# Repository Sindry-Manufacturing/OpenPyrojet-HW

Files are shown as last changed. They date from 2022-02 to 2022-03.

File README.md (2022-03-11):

# OpenPyrojet-HW
This is a repository for the hardware components of the OpenPyrojet 3D printer project. 
The current objective of OpenPyrojet, is  to create the first generation Open source/hardware/software thermal spraying 3D printer. 
In short, by using affordable, accessible and readily available parts and materials, we will create a new breed of 3D printer, that enables the heterogenous additive manufacturing of metal, plastic and ceramic monoliths rapidly, precisely, autonomously and at relatively low cost(in terms of time and money) to the user compared to contemporary 3D printing solutions. 

We believe this to be possible, due to the convergence of several co-factors in the present day(2022). In particular, the incredible decline in cost and complexity of autonomous CNC and robotic components, in terms of control and actuation, as well as the wide availability of good quality standard structural elements, the decreasing cost of refractory materials in favorble form factors, the wide availability of energy dense fuel products, and the increasing availability and declining cost of particulate material feedstocks. 
Additionally, the need for low cost, autonomous and widely accessible electronics prototyping and manufacturing processes, that improve on the user experience and the overall dirty dull and dangerous state of the art in electronics manufacturing are highly desirable to many parties beyond just we the developers. Current 3D printing approaches are largely ineffective in terms of cost and time for generating high quality, looks like, feels like, and works like, electronic parts, we believe this represetns a substantial opportunity to create change in electronics manufacturing and prototyping, and eventually in the whole of manufacturing as a concept through the introduction of relatively low cost, autonomous, high speed, high precision 3D printing of metals, plastics and ceramics. 
We also aim to eventually bring totally custom, free open and autonomous, on demand manufacturing, to the consumer desktop, or at least to the community scale, facilitating a return to the flexible and local cottage industries of the past, now cybernetically enhanced with the ability to create with the speed and quality of autonomous mass production assembly lines, and accelerated by the computerization and networked intelligence of the modern internet. 

We believe we can accomplish these lofty goals by hybridizing thermal inkjet printing and thermal spray tehnologies into a compact, self contained, open source 3D printer print head assembly and material feedstock handling system integrable with mass market consumer 3D printer control boards and robotic motion systems such as the Ender 3, the Prusa mk3s and mini, and others. 

The basic system concept is thus:
Fuel and material are held in a reservoir, kept mixed and pumped in and out by a syringe pump. This pump pushes fuel, and suspended material particles to the print head from the back through perfboard(of which the print head is made) holes. The fuel and material mixture circulate over the top of the print head at a constant average velocity to produce a negative pressure and prevent settling of the materials suspended in the fuel.
When the time comes to deposit material on the build plate, a short voltage pulse of controlled amplitude is applied to the captive heater wire, across two adjacent plated through vias in the perfboard.  This causes the wire to rapidly(with in 1-10 milliseconds) heat up, vaporizing the fuel and entraining the suspended material. 
Once an appropriate volume of fuel and material has been vaporized into the nozzle, a second, larger amplitude voltage pulse is applied, raising the temperature in the nozzle to the autoignition temperature of the fuel/air mixture in the nozzle. This ignites the fuel-air mixture, and melts and accelerates the material to deposit it on the build plate. Thusly, can we deposit virtually any material known, heterogenously, autuonomously with nearly complete closed loop control of the mass and energy flows of the process. 
Control is achieved by continuously performing 3 simultaneous measurement techniques, namely, differential scanning calorimetry(DSC), Surface enhanced IR spectroscopy(IRSPEC), and cyclcic voltammetry(CV). 
The first technique(DSC) is done by continuously monitoring the relationship between temperature, and power of the heating element throughout the deposition process. By tracking changes in the power applied to the element to maintain a given temperature across the whole temperature ramp during deposition, we can spot phase changes, ignition, deflagration and combustion, and continuously monitor the health and efficiency of the deposition proces in each nozzle during each discrete deposition event.  
The second technique (IRSPEC) is done by continuously monitoring the short time scale photocurrents induced in the element by the emitted and reflected ir-photons fromthe combustion ofthe fuel, the melting and cooling of the feed stock material and from te various surfaces effected during deposition. This allows us to monitor the chemical composition of the involved surfaces in real time, and to get a handle on the specic bonding events taking place to allow tunig and monitoring of interface growth and quality during deposition.
The third technique(CV) is done by providing a controlled input voltage waveform, and continuously monitoring changes in the response current of the heating element and adjoining electrical contacts. In this way we can detect electrochemical events and manipulate the electrochemistry of the combustion, and gaseous phases in the vicinity of the deposition process, in particular, oxidation events, reduction events, partial combustion, coking, etc.

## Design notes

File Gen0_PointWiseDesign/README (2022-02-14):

This is a repository dedicated to hardware for FDM printer mods that enable direct printing of metal, plastic, and ceramic through conventional FDM style cartesian printers and their associatedpoint wise scanning design.
Essentially, we pump air through a carburetor which contains metal/ceramic/plastic loaded fuel (ethanol, gasoline etc.) this entrains particles of the material in droplets of the fuel into the pumped airstream and sends them to 
a conventional E3D extruder hotend which ignites the fuel mixture and enables a continuous flame spray like deposition process, controlled by an FDM printer cartesian stage to form 3D dimensional objects in a continuous machine path, layer by layer.

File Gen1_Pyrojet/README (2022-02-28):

This is a repository for images, video and information regarding th first generation (96 DPI) FR4 based inkjet style pyrojet printer built on a modified ender3 platform. 
This includes hardware design guides, introductory texts on the construction and operation of the system and in depth technical data reagarding materials, lifetime, and printing capabilities. 

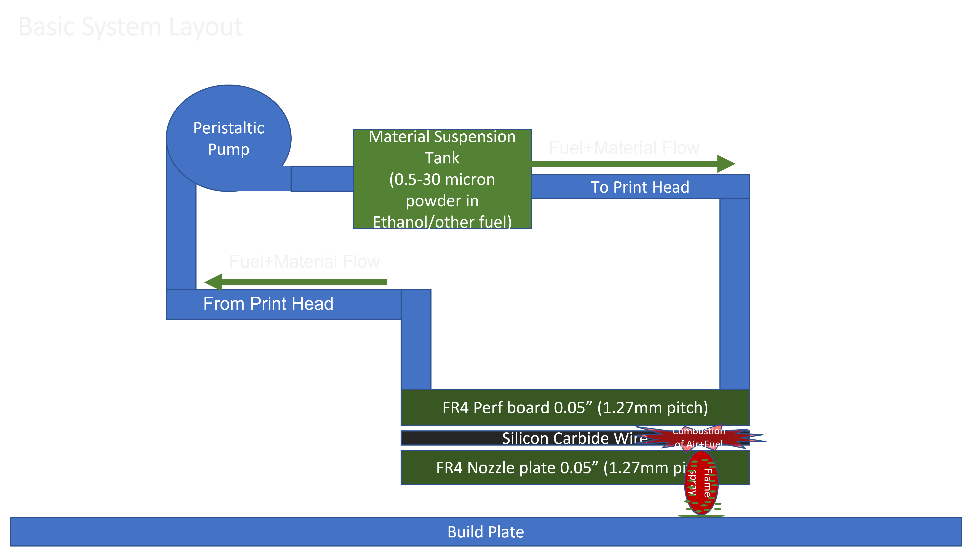
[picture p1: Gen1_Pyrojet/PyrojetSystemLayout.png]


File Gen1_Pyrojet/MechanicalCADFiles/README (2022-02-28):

This is where you can find the adapters for the generation 1 pyrojet print head. It is designed to be adaptable to the main gantry plate of the Ender 3 FDM 3D printer from creality.

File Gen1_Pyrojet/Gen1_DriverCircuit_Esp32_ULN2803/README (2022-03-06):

This is a directory for images and CAD files relating to the driver electronics for the first generation Pyrojet print head

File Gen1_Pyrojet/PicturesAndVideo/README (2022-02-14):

This is a directory for containing images and video of the generation 1 inkjet style pyrojet print heads.

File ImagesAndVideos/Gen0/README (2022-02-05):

This is a directory of the old images and videos pertaining to the Generation 0 print head design...

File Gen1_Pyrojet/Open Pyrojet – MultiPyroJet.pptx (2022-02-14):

## Open Pyrojet – MultiPyroJet

FDM printer modified to print metal, ceramic and high temperature plastics, with enhanced resolution, automation, control and speed.

## Basic System Layout

Build Plate

Peristaltic Pump

Material Suspension Tank
(0.5-30 micron powder in Ethanol/other fuel)

Fuel+Material Flow

To Print Head

Fuel+Material Flow

From Print Head

FR4 Perf board 0.05” (1.27mm pitch)

Silicon Carbide Wire

FR4 Nozzle plate 0.05” (1.27mm pitch)

Combustion of Air+Fuel

Flame spray

## Print Head Detail

The print head is made with an FR4 pefboard as the backplate, serving as electrical connection and mechanical support to a silicon carbide wire. This wire, once mechanically clamped across the plated through holes in the perfboard, via compression by a milled FR4 copper clad nozzle plate, acts as a heating element that ejects fuel and material through the milled nozzles.

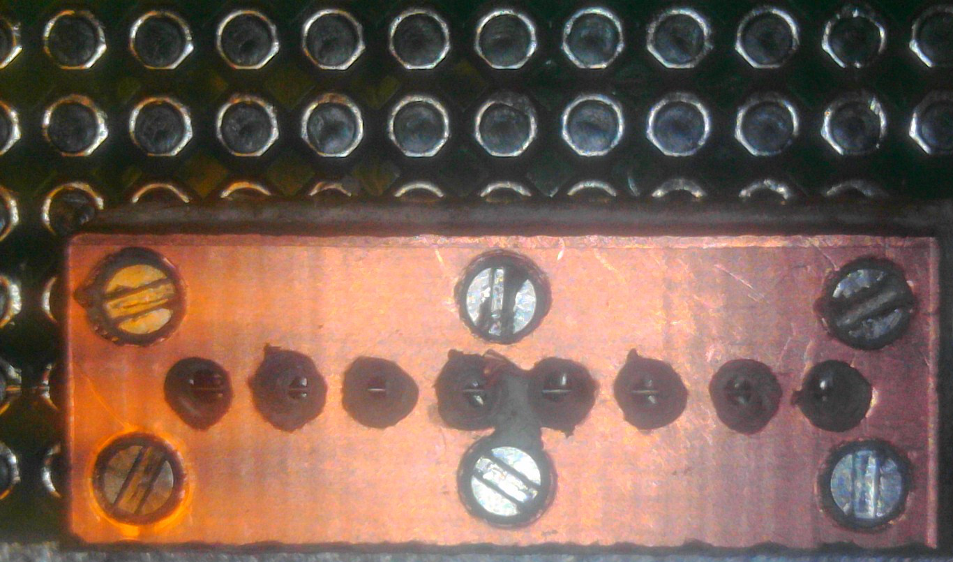
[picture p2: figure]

1.27 mm Perf Board

CNC milled copper clad FR4 nozzle plate

Silicon Carbide Wire

0.3mm Nozzle

M0.6X4mm Screw

0.65mm diameter hole, 1mm pad diameter

## Basic System Description_MultiPyrojet-

1. Fuel and material are held in a reservoir, kept mixed and pumped in and out by a single peristaltic pump. This peristaltic pump pushes fuel, and suspended material particles to the print head from the back through the perfboard holes. The fuel and material mixture circulate over the top of the print head at a constant average velocity to produce a negative pressure and prevent leakage from the print head.
2. When the time comes to deposit material on the build plate, a short voltage pulse of controlled amplitude is applied to the captive silicon carbide wire, across two adjacent plated through vias in the perfboard. This causes the wire to rapidly heat up, vaporizing the fuel and entraining the suspended material.
3. Once an appropriate volume of fuel and material has been vaporized into the nozzle, a second, larger amplitude voltage pulse is applied, raising the temperature in the nozzle to the autoignition temperature of the fuel/air mixture in the nozzle. This ignites the fuel-air mixture, and melts and accelerates the material to deposit it on the built plate.

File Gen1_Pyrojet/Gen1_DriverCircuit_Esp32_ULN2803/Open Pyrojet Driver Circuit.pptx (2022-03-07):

## Open Pyrojet Driver Circuit

By Michal Lynn

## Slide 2

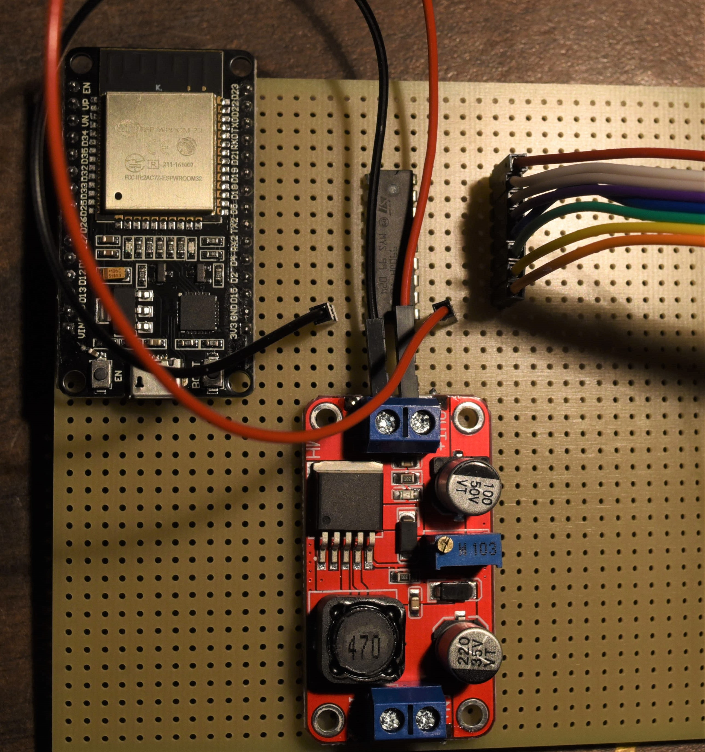
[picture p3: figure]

ESP 32

ULN2803A Darlington array

XL6019 Converter

Outputs

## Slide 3

Datasheets for assorted components-

https://www.ti.com/product/ULN2803A
https://datasheetspdf.com/pdf/839862/Xlsemi/XL6019/1
https://www.google.com/url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
https://www.mouser.com/datasheet/2/58/BPS-DAT-(ST3U)-Datasheet-771561.pdf

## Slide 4

Datasheets for assorted components-

Print Head

SiC Filament

ESP32

3-5 V Digital PWM Output

ULN2803A
(2)

+ 40 Volts

Ground

XL6019

+ 12/24 Volts

Ground

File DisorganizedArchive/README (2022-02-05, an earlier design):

This is a directory of all the old files and iterations on the way to version 1 hardware...This is only provided for reference material for curious adventurers, and as reference materials for future iterations...

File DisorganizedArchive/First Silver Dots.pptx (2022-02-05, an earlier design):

## First Silver Dots

10% mass loading of silver in 90% WD-40
1-3 Micron average diameter silver particles
Printed with ~12 watts of peak input power (manually controlled)

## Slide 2

0.75mm

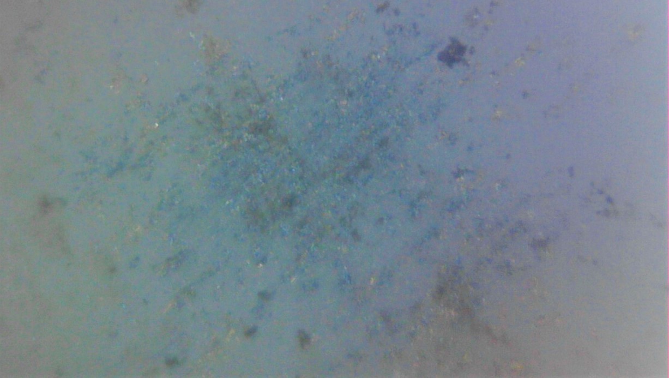
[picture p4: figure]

< 10 micron thick Silver deposit

0.75mm

Al2O3 Substrate

Single pulse deposit

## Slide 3

1.5mm

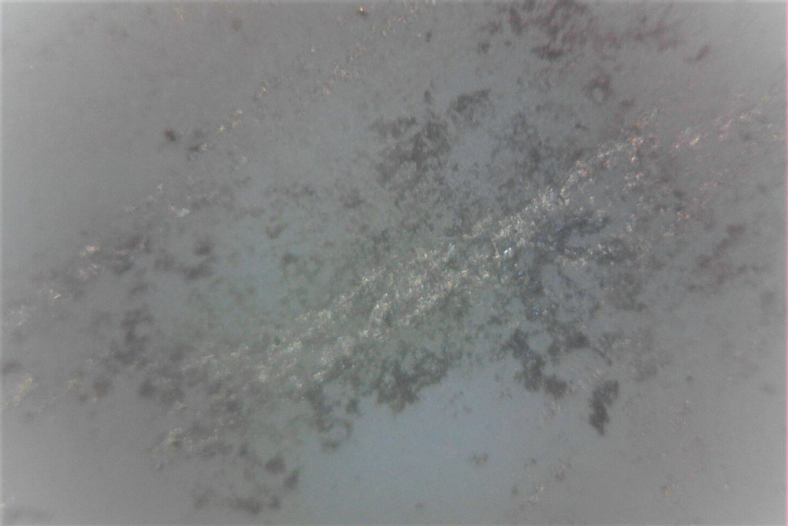
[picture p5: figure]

Steel needle scratch zone

< 10 micron thick Silver deposit

1.0mm

Al2O3 Substrate

Two pulse deposit

Print Direction

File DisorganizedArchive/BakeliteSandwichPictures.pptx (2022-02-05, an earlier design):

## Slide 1

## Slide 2

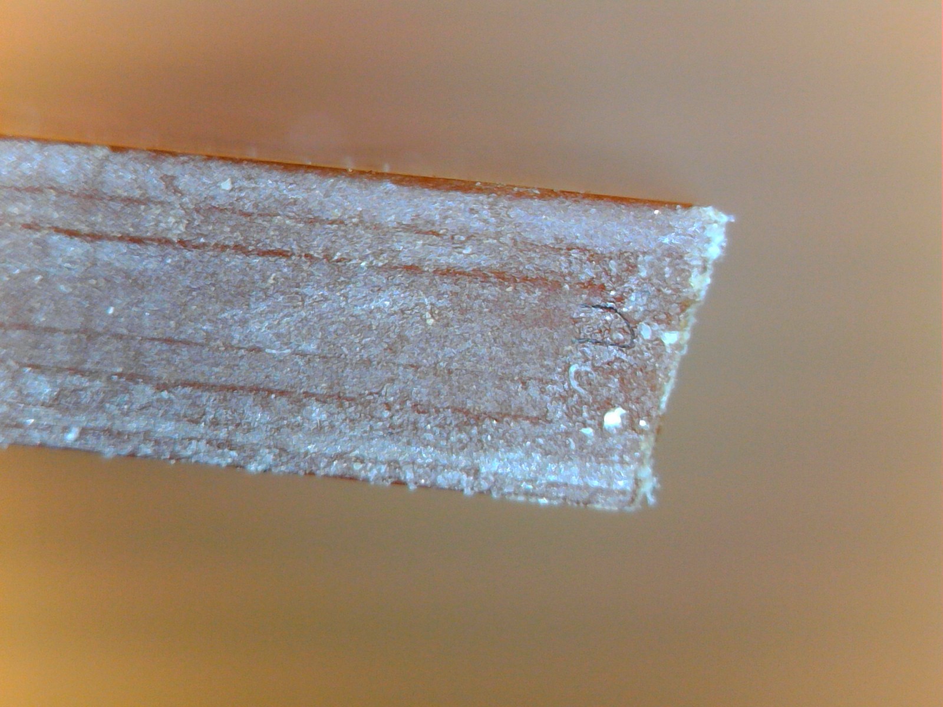
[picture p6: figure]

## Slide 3

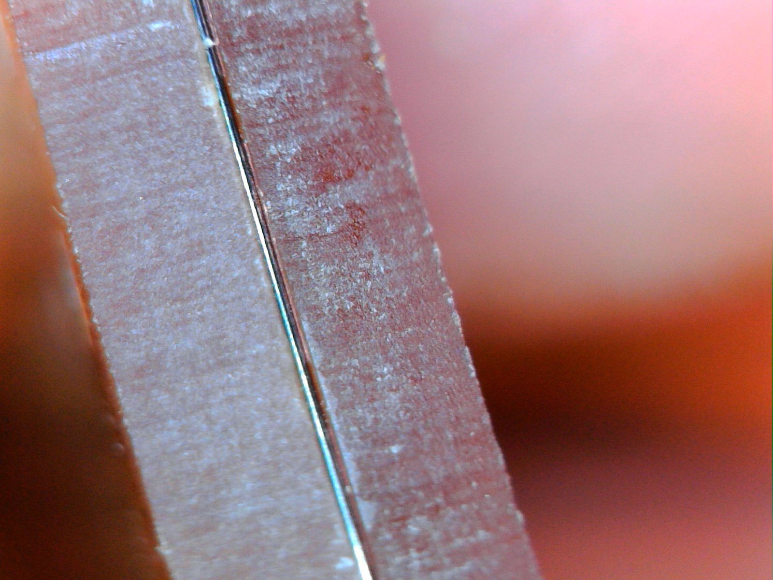
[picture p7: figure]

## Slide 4

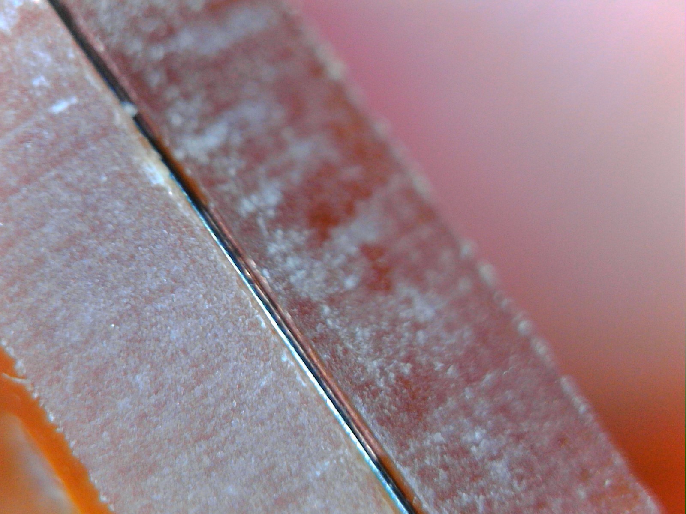
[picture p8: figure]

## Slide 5

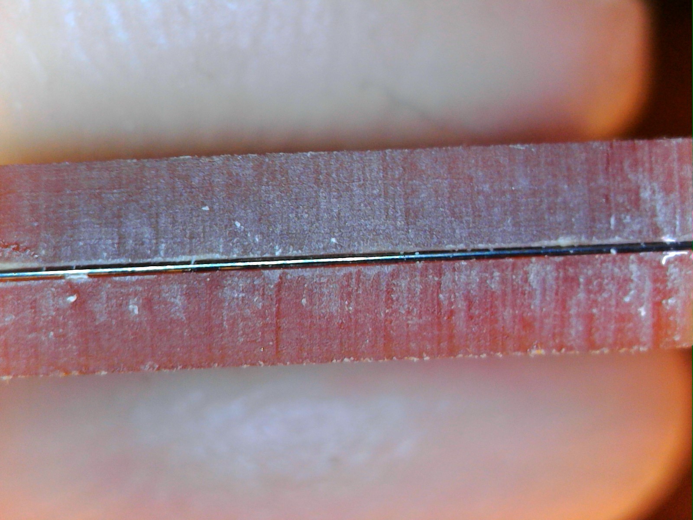
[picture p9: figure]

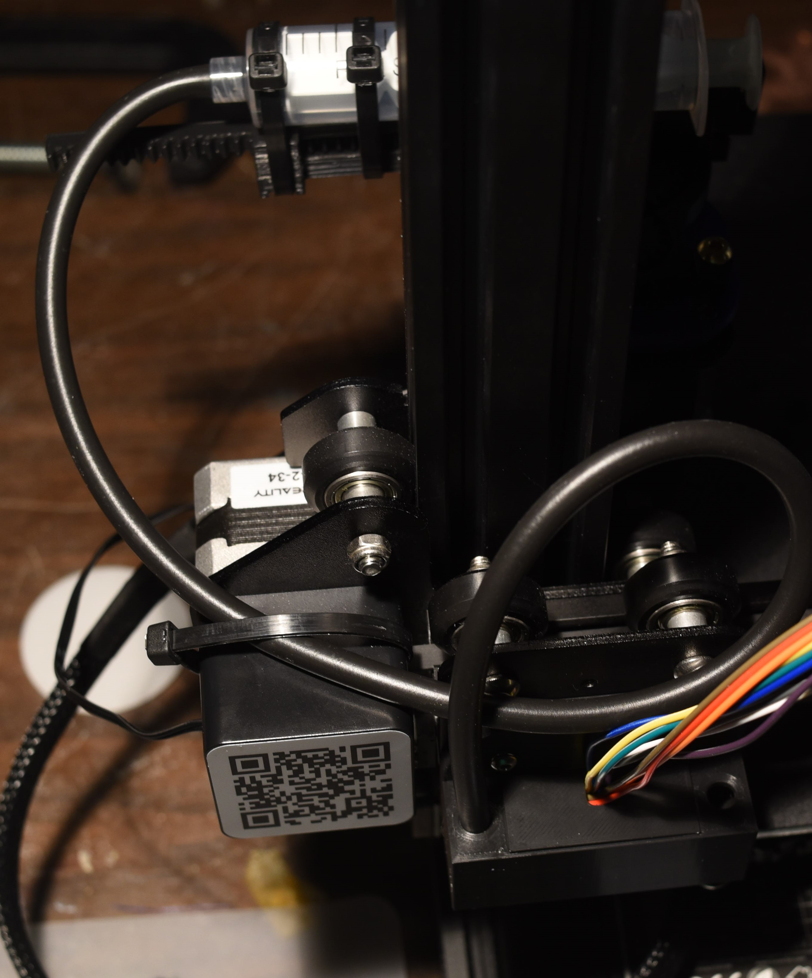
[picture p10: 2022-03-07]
Gen1_Pyrojet/MechanicalCADFiles/SyringePumpFuelController_4.jpg

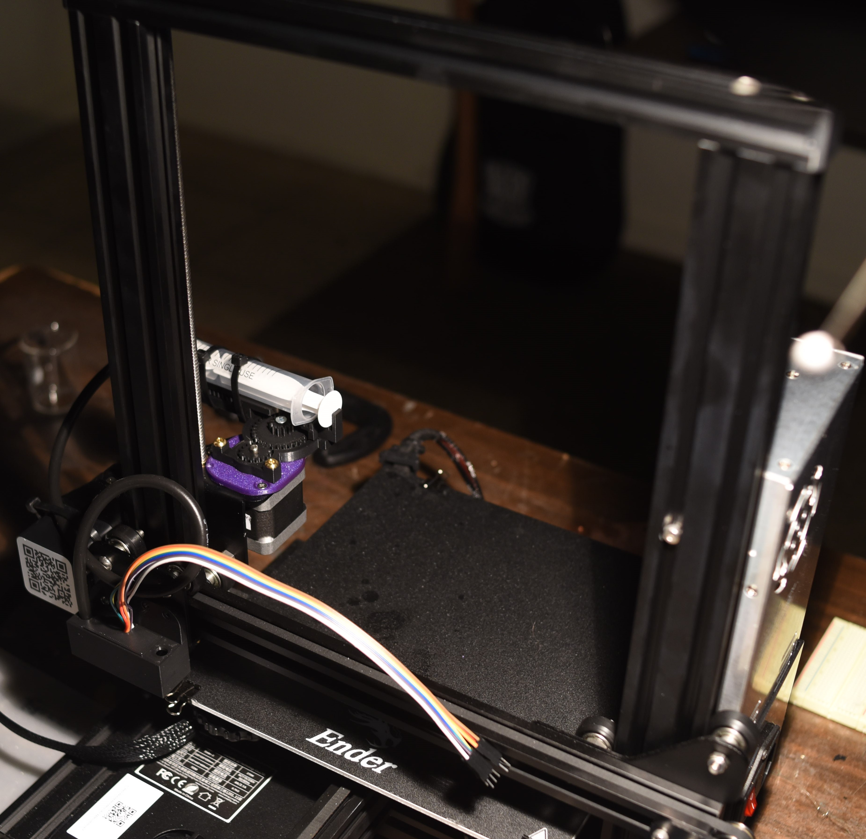
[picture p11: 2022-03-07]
Gen1_Pyrojet/MechanicalCADFiles/SyringePumpFuelController_5.jpg

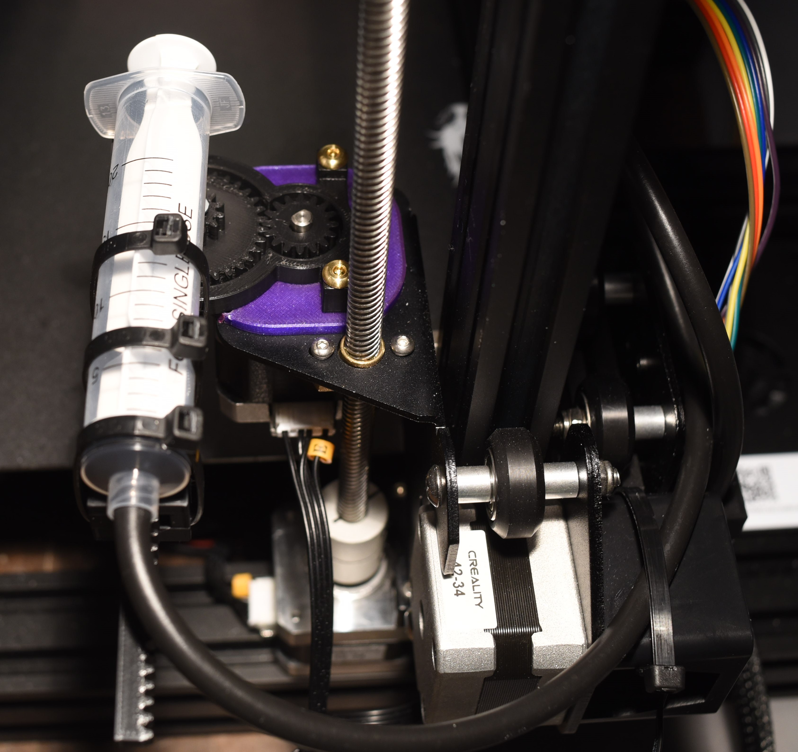
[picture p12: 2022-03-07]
Gen1_Pyrojet/MechanicalCADFiles/SyringePumpFuelController_3.jpg

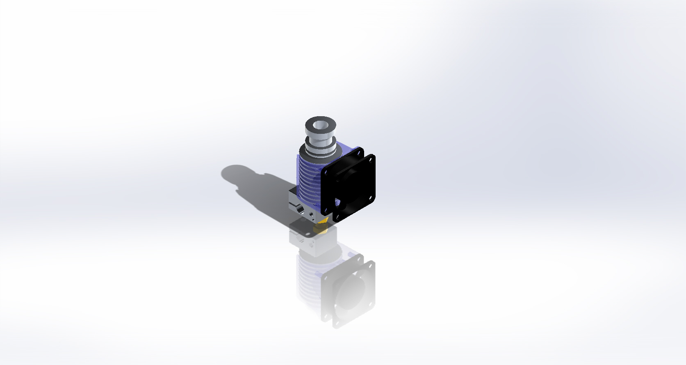
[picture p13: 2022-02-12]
Gen0_PointWiseDesign/e3d v6.JPG

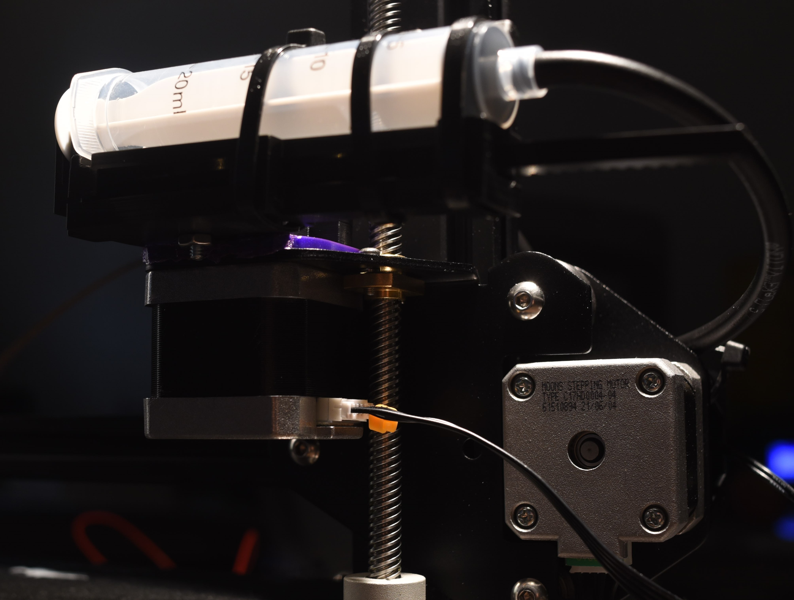
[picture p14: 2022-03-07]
Gen1_Pyrojet/MechanicalCADFiles/SyringePumpFuelController_2.jpg

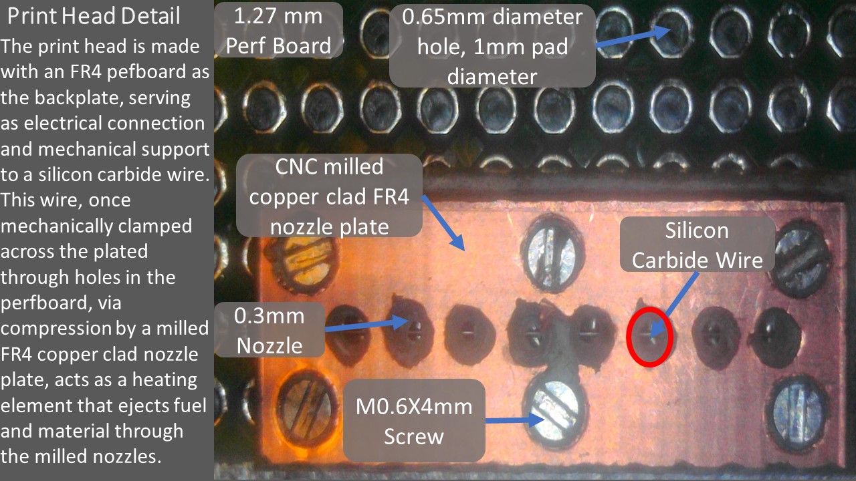
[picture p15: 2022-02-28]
Gen1_Pyrojet/PicturesAndVideo/CloseupOfNozzlePlateOverview.JPG

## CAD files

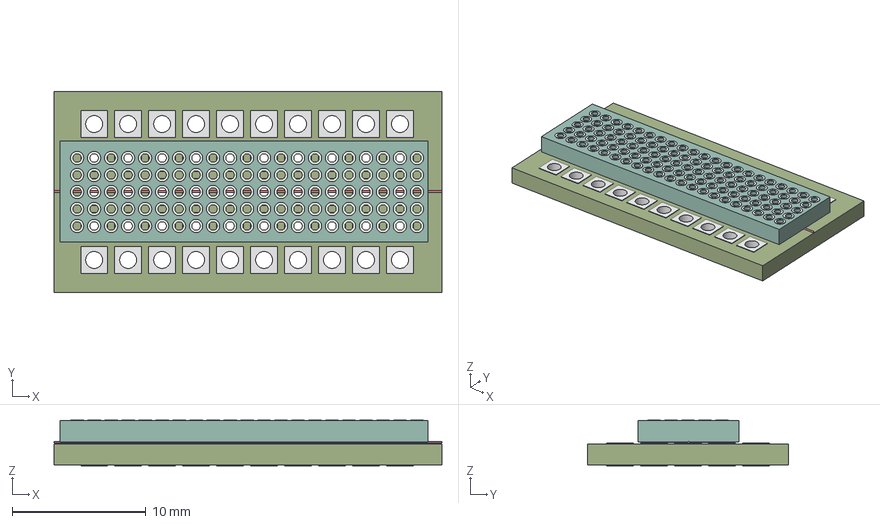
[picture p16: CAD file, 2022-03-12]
Gen1_Pyrojet/MechanicalCADFiles/PrintheadV1Assembly1.stp
29.0 x 15.0 x 3.41 mm
2.54mmPitchPerfboardBackplane
1.27mmNozzlePlate
SiCFilamentRed

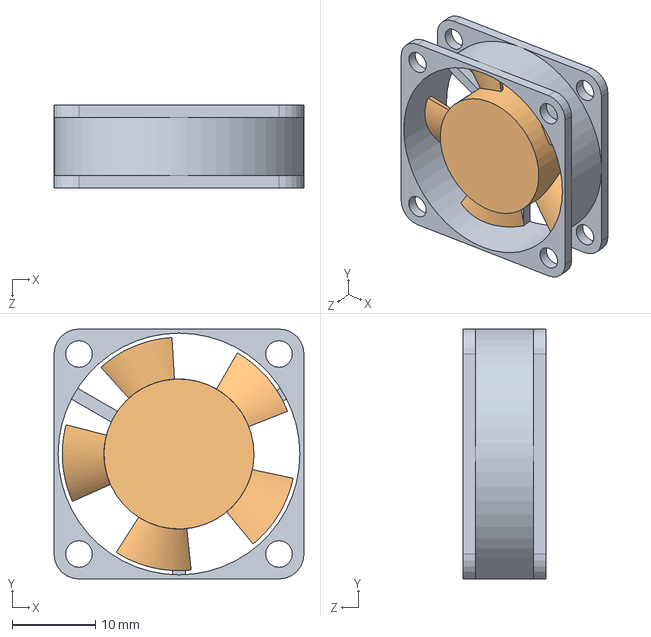
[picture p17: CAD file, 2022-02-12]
Gen0_PointWiseDesign/fan.SLDASM
30.0 x 30.0 x 10.0 mm
fan sub1
fan sub2

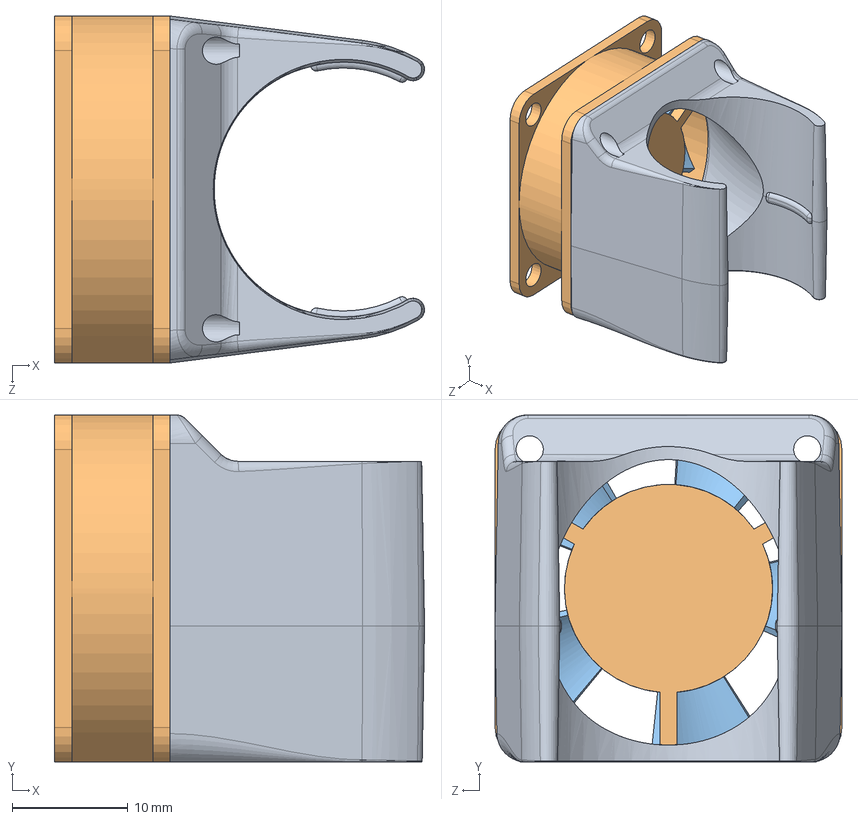
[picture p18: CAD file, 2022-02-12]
Gen0_PointWiseDesign/fanduct.SLDASM
32.0 x 30.0 x 30.0 mm
fan duct
fan sub1
fan sub2

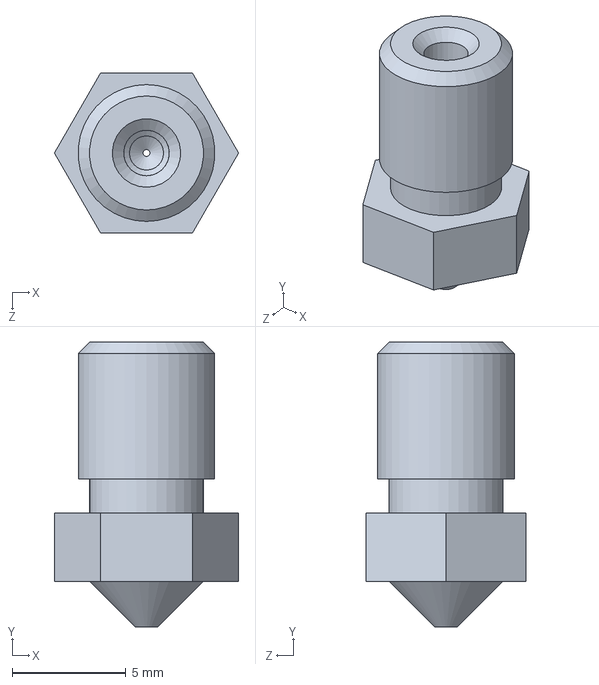
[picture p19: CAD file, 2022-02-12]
Gen0_PointWiseDesign/e3d nozzle (0.3).SLDPRT
8.08 x 12.5 x 7.00 mm

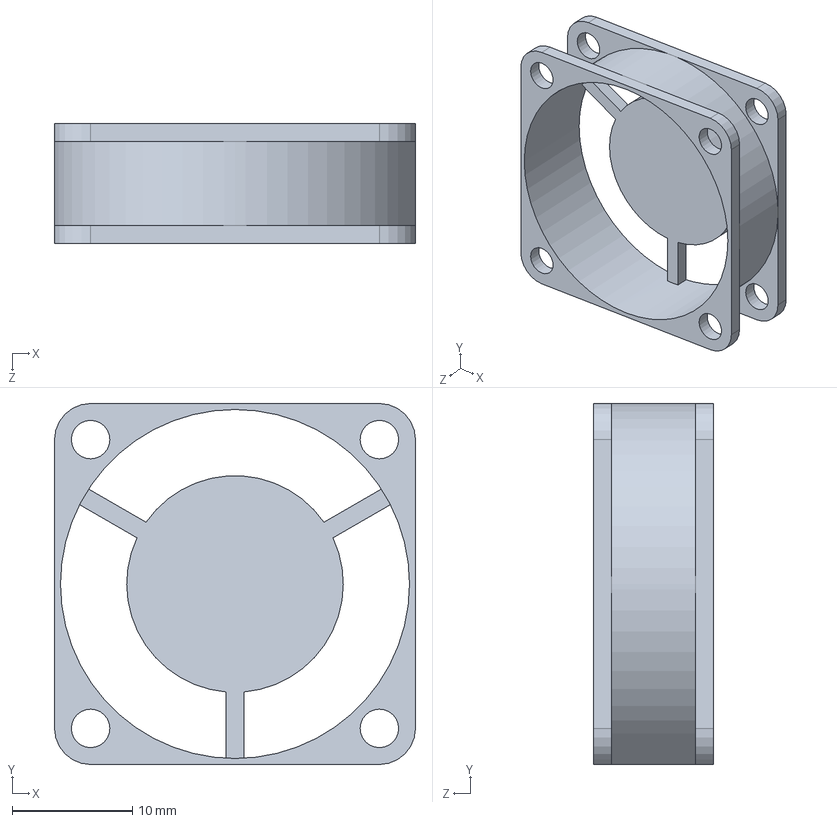
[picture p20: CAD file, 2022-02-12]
Gen0_PointWiseDesign/fan sub1.SLDPRT
30.0 x 30.0 x 10.0 mm

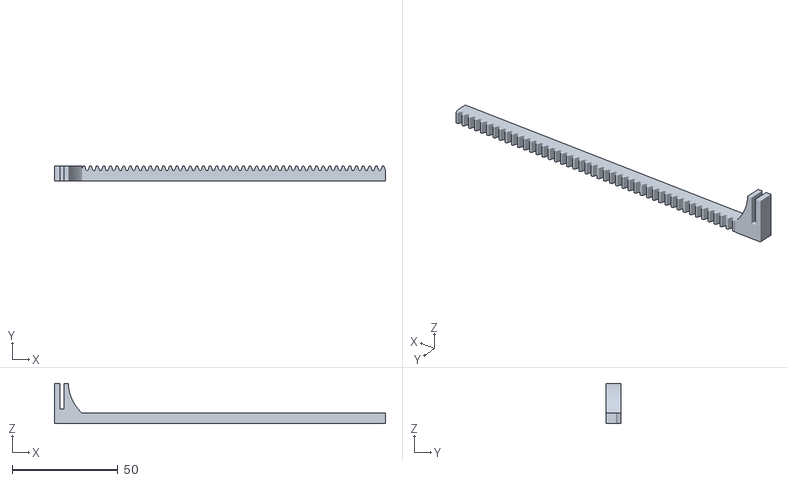
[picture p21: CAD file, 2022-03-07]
Gen1_Pyrojet/MechanicalCADFiles/rack.stl
156.4 x 7.00 x 19.0

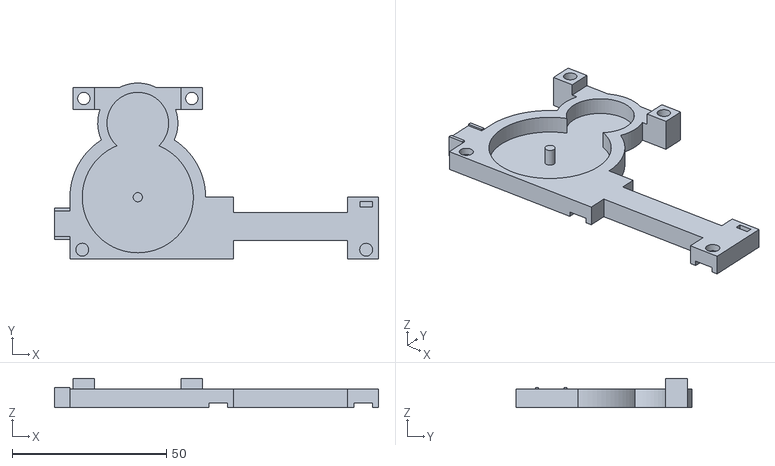
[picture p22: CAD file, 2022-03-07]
Gen1_Pyrojet/MechanicalCADFiles/lower_body.stl
105.0 x 57.0 x 9.50

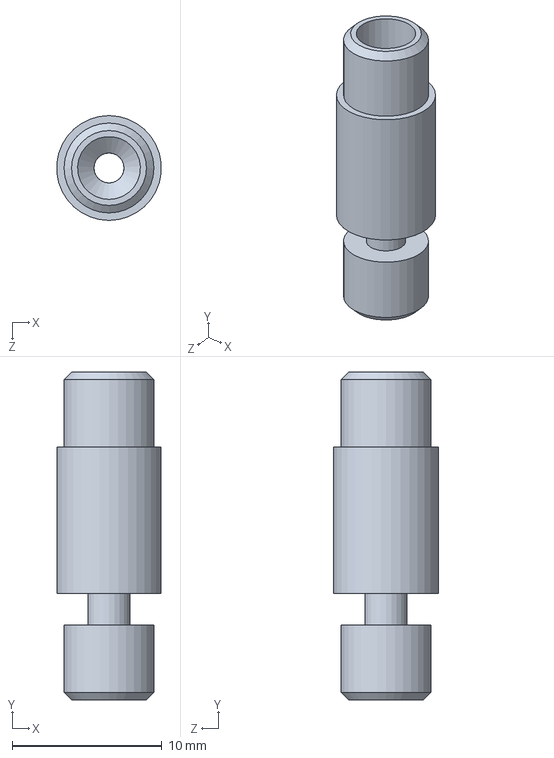
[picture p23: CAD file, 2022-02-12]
Gen0_PointWiseDesign/e3d heat break.SLDPRT
6.97 x 21.9 x 7.00 mm

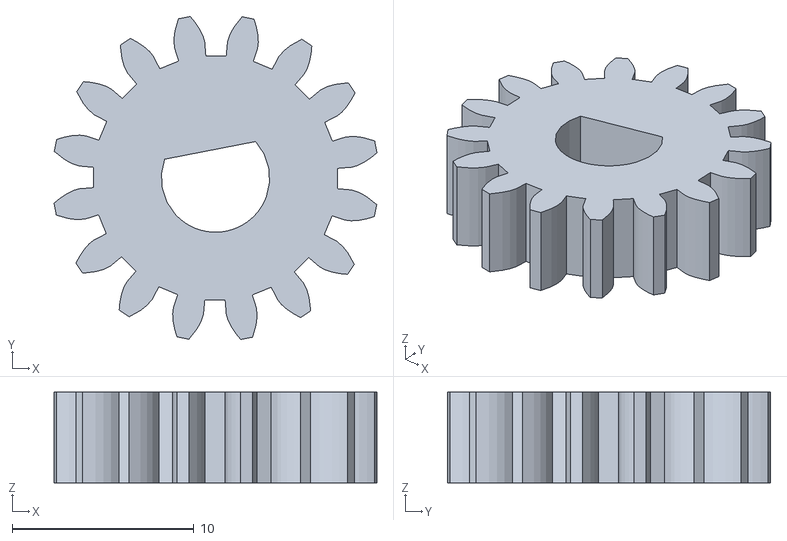
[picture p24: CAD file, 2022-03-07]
Gen1_Pyrojet/MechanicalCADFiles/motor_gear _NEMA17v2.stl
17.8 x 17.8 x 5.00

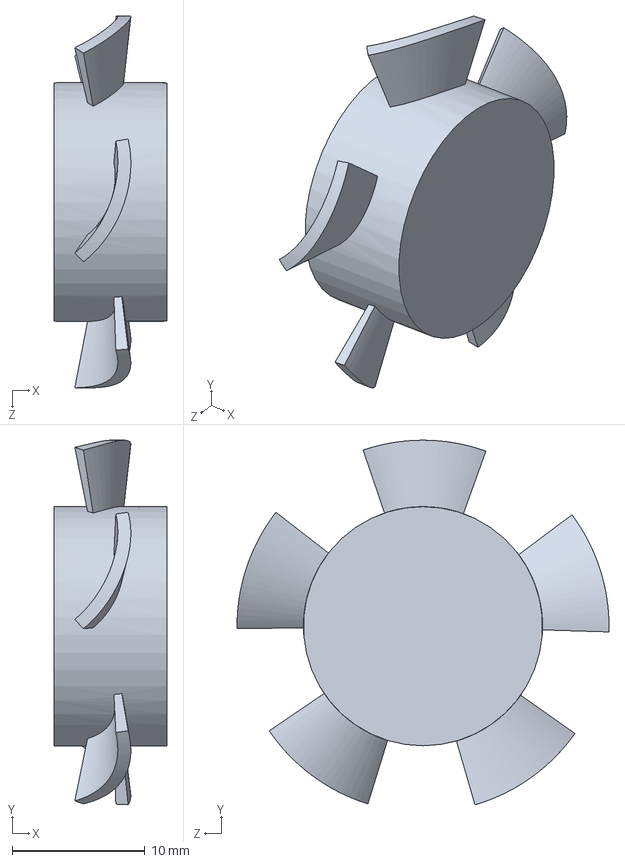
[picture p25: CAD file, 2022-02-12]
Gen0_PointWiseDesign/fan sub2.SLDPRT
8.50 x 27.4 x 28.0 mm

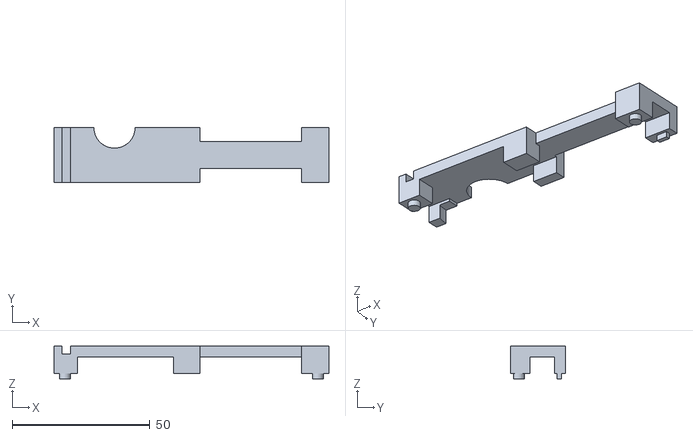
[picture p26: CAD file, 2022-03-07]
Gen1_Pyrojet/MechanicalCADFiles/upper_body.stl
100.0 x 20.0 x 12.0

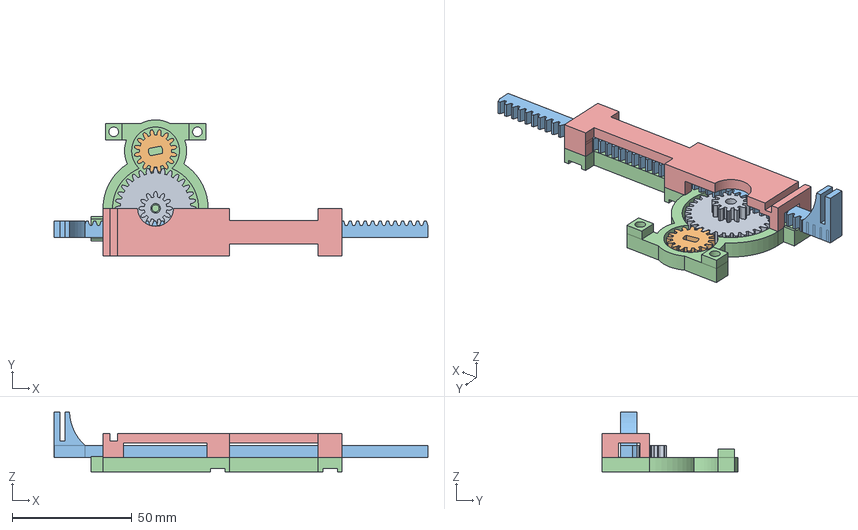
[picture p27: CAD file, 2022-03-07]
Gen1_Pyrojet/MechanicalCADFiles/pump_final_1.fcstd
156.4 x 57.0 x 25.0 mm
transmisson
motor_gear
grip
lower_part001

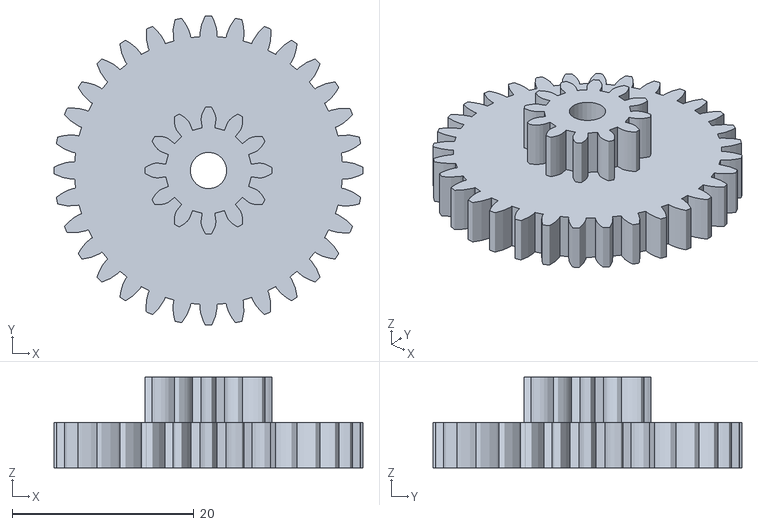
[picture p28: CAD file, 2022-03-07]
Gen1_Pyrojet/MechanicalCADFiles/transmission.stl
34.0 x 34.0 x 10.0

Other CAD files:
Gen0_PointWiseDesign/e3d nozzle (0.4).SLDPRT
Gen0_PointWiseDesign/e3d nozzle (0.6).SLDPRT
Gen0_PointWiseDesign/e3d nozzle (0.2).SLDPRT
Gen1_Pyrojet/MechanicalCADFiles/motor_gear_modified.stl
Gen0_PointWiseDesign/e3d nozzle (0.5).SLDPRT
DisorganizedArchive/1.27mmPitchProtoboard_nozzlePlate.0013.ipt
DisorganizedArchive/1.27mmPitchProtoboard_nozzlePlate.ipt
DisorganizedArchive/1.27mmPitchProtoboard_nozzlePlate.stl
DisorganizedArchive/1.27mmpitchProtoboardDesign.0005.ipt
DisorganizedArchive/1.27mmpitchProtoboardDesign.ipt
DisorganizedArchive/1.27mmpitchProtoboardDesign.ipt_.25inch_.25Inch.0003.ipt
DisorganizedArchive/1.27mmpitchProtoboardDesign.ipt_.25inch_.25Inch.ipt
DisorganizedArchive/1.27mmpitchProtoboardDesign.ipt_.25inch_.25Inch_MIR.ipt
DisorganizedArchive/1.27mmpitchProtoboardDesign.ipt_.25inch_.25Inch_MIR1.ipt
DisorganizedArchive/2.54mmpitchProtoboardDesign_10milheaterwidth.0001.ipt
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

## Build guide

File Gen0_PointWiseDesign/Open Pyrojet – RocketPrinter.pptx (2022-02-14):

## Open Pyrojet – RocketPrinter

FDM printer modified to print metal, ceramic and high temperature plastics, without compromising resolution and speed.

## Basic System Layout

Air Induction
(Air Pump)

Material Feed Venturi

FDM Printer Bowden Tube to standard hot-end

Valve

Material Suspension Tank
(0.5-30 micron powder in Ethanol/other fuel)

## Basic System Layout

Air Induction
Peristaltic Pump

Material Feel Peristaltic Pump

Material Feed Venturi

FDM Printer Bowden Tube to standard hot-end

## Basic System Layout

Build Plate

Combustion of Air+Fuel

Air+Fuel+Material Flow

FDM Printer Bowden Tube to standard hot-end

Heat sink

Heat Block

Material Melts

Heat Break

Flame spray

## Basic System Description-

1. Air is pulled from atmosphere and forced through a venturi which generates a vacuum that entrains and atomizes fuel and suspended materials from a tank.
2. This air/fuel/material mixture is fed through the Bowden system of a standard FDM printer such as an ender3 or prusa mini, ultimately to arrive at the hotend for ignition.
3. The hotend heater and block achieve the autoignition temperature of the air/fuel/material mixture and start it combusting through the extruder nozzle.
4. The combustion process accelerates the mixture out the nozzle, melts the entrained material particles and consumes the oxygen in the nozzle and air gap between nozzle and build plate.
5. The now molten particles surrounded by combustion byproducts deposit on the build plate and form a part, layer by layer, in the same fashion as FDM.

## Basic System Description_PeristalticPumps-

1. Air is pulled from atmosphere and forced through a venturi and mixing chmber where fuel is injected via a similar peristaltic pump drawing from a suspension of particles in fuel. This air/fuel/material mixture is fed through the Bowden system of a standard FDM printer such as an ender3 or prusa mini, ultimately to arrive at the hotend for ignition.
2. The hotend heater and block achieve the autoignition temperature of the air/fuel/material mixture and start it combusting through the extruder nozzle.
3. The combustion process accelerates the mixture out the nozzle, melts the entrained material particles and consumes the oxygen in the nozzle and air gap between nozzle and build plate.
4. The now molten particles surrounded by combustion byproducts deposit on the build plate and form a part, layer by layer, in the same fashion as FDM.
